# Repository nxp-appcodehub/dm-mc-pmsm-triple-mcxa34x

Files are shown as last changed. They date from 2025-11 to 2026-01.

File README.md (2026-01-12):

# NXP Application Code Hub
[](https://www.nxp.com)

## MCX A34x Triple-Motor and Interleaved PFC Control using an HVP Board

This demo describes the implementation of sensorless triple motor FOC on NXP MCXA346 MCU. Please refer to [AN14805](https://docs.nxp.com/bundle/AN14805/page/topics/introduction.html) for complete instructions on how to use this software. 

#### Boards: X-MCXA346-3MC, dual-motor adapter board
#### Categories: Motor Control
#### Peripherals: PWM, ADC
#### Toolchains: MCUXpresso IDE

## Table of Contents
1. [Software](#step1)
2. [Hardware](#step2)
3. [Setup](#step3)
4. [Results](#step4)
5. [FAQs](#step5) 
6. [Support](#step6)
7. [Release Notes](#step7)

## 1. Software
- Download and install [MCUXpresso IDE V25.06 or later](https://www.nxp.com/design/design-center/software/development-software/mcuxpresso-software-and-tools-/mcuxpresso-integrated-development-environment-ide:MCUXpresso-ID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).
- Download and install the latest version of [FreeMASTER](https://www.nxp.com/design/software/development-software/freemaster-run-time-debugging-tool:FREEMASTER)(3.2.2.2).
- Download the code from Git repository dm-mc-pmsm-triple-mcxa34x.  
- MCUXpresso for Visual Studio Code: This example supports MCUXpresso for Visual Studio Code, for more information about how to use Visual Studio Code please refer [here](https://www.nxp.com/design/training/getting-started-with-mcuxpresso-for-visual-studio-code:TIP-GETTING-STARTED-WITH-MCUXPRESSO-FOR-VS-CODE).

## 2. Hardware
- X-MCXA346-3MC
- 2 pcs [FRDM-MC-LVPMSM](https://www.nxp.com/design/development-boards/freedom-development-boards/mcu-boards/nxp-freedom-development-platform-for-low-voltage-3-phase-pmsm-motor-control:FRDM-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).
- 2 [LINIX 45ZWN24 Motor](https://www.nxp.com/design/development-boards/freedom-development-boards/mcu-boards/low-voltage-3-phase-motor-for-frdm-platform:FRDM-MC-LVMTR).
- 1 pcs dual-motor adapter board
- 1 DL71-PS11M2-1.5K PMSM High-Voltage motor

- Personal Computer
- USB type-C cable and 24V adaptors × 2.

## 3. Setup
### 3.1 Import project
#### 3.1.A Import project from Application Code Hub
1. Open MCUXpresso IDE, in the Quick Start Panel, choose **Import from Application Code Hub** 
2. Found demo you need by searching the name directly or selecting tags you interested in. Open the project, click the **GitHub link** to then **Next**. 
3. Select **main** branch and then click **Next**.
4. Select your local path for the repo in **Destination->Directory:** window. The MCUXpresso IDE will clone the repo to the path that your selected, **Next** after the clone process.
5. Select **Import existing Eclipse projects** in **Wizard for project import** window then **Next**. 
6. Select the project in this repo(only one project in this repo) then **Finish**. 
#### 3.1.B Import project after clone git repo to your local path
1. Clone repo **dm-mc-pmsm-triple-mcxa34x ** from **GitHub**. Open MCUXpresso IDE, in the Quick Start Panel, choose **Import project(s) from file system** .
2. Select your local path of the repo in **Project directory(unpacked)** item then **Next**. If you download a compressed pack from GitHub, Select your local path of the package in **Project archive(zip)** item.
3. Select the project in this repo(show in **Projects:** window, only one project in this repo), then **Finish**. . The project will be pasted to your IDE workspace if you click **Copy projects into workspace** in **Options** item, the change you made will be saved in the copy in workspace.
#### 3.1.2 Then you will see the project in **Project Explorer** window.
### 3.2 Compiler the project

This project contains 3 configurations, **Debug**, **Release** and **Debug_SRAMX**. **Release** configuration has a standalone link script to allocate frequently called code in SRAMX to improve performance. **Right click** the project name in **Project Explorer** window, and select **Properties** to open properties window. Open **Manage Configurations**, select configuration you want to use then **Set Active**.  
 
Use build botton in toolbar to compiler the project.  

### 3.3 Hardware setup
#### 3.3.1 Connect the motor and power shield board.
 Connect the 3-phase wire of the **first motor** to the **J7** connector on the **first FRDM-MC-LVPMSM** according to phase sequence (**White** wide--phase**A**; **Bule** wide--phase**B**; **Green** wide--phase**C**). Repeat the same steps for the **second motor** and **second FRDM-MC-LVPMSM**.

#### 3.3.2 Combine the motor kit with adaptor board.
Connect the **first FRDM-MC-LVPMSM** board to the **J1_M1~J4_M1** arduino connector of the **NXP Dual Motor Adaptor Board**. And connect the **second FRDM-MC-LVPMSM** board to the **J1_M2~J4_M2** arduino connector of the adaptor board. The **X-MCXA346-3MC** daughter board **J9 and J8** is connected to the **2 IDC-20Pin socket** on the adaptor board. The GERBER file and schematic of the adaptor are in path **dm-mc-pmsm-triple-mcxa34x/schematic_pcb**.

#### 3.3.3 Rework
Rework HVP board resistor **R128** to **680Ω**

#### 3.3.4 Connect daughter board and High-Voltage motor to HVP
Connect X-MCXA346-3MC daughter board to HVP board PCI socket, connect High-Voltage motor to HVP J13.

#### 3.3.5 Download and Power up
Power 2 FRDM-MC-LVPMSM boards with two 24V adaptor.  
Use a USB cable to connect to the X-MCXA346-3MC board via **J2** Download the code using debug button in tool bar after compiler. Select **CMSIS-DAP** in **Debug As** according firmware in your on-board debugger. Then unplug the USB cable and power up the HVP board with AC 220V power line.

### 3.4 Run the demo
Connect HVP board with PC through USB plugged on  **J4** on **HVP** to control the **Motor M1~M3** to run or stop, use FreeMASTER project **"pmsm_float.pmpx"** in the package path **"dm-mc-pmsm-triple-mcxa34x\motor_control\freemaster"** to control the motor, change rotor speed and obverse the speed or other value. 
## 4. Results

Memory Usage:
|Debug Configuration|Flash Usage|SRAM usage|SRAMX usage|
|:----:|:----:|:----:|:----:|
|All code in Flash|65.9 KB|30.3 KB|0 KB|
|Partial code in SRAM/SRAMX |66.3 KB |35.2 KB | 4.4 KB |

CPU loading:
|Debug Configuration|Flash Usage|SRAM usage|SRAMX usage|
|:----:|:----:|:----:|:----:|
|All code in Flash|65.38 %|2.98 %|68.36 %|
|Partial code in SRAM/SRAMX |30.09 %|1.14 %|31.23 %|

## 5. Support

#### Project Metadata

<!----- Boards ----->

<!----- Categories ----->


<!----- Peripherals ----->



<!----- Toolchains ----->


Questions regarding the content/correctness of this example can be entered as Issues within this GitHub repository.

>**Warning**: For more general technical questions regarding NXP Microcontrollers and the difference in expected functionality, enter your questions on the [NXP Community Forum](https://community.nxp.com/)






## 7. Release Notes
| Version | Description / Update | Date |
|:---:|---|---:|
| 1.0 | Initial release on Application Code Hub | November 11<sup>th</sup> 2025 |

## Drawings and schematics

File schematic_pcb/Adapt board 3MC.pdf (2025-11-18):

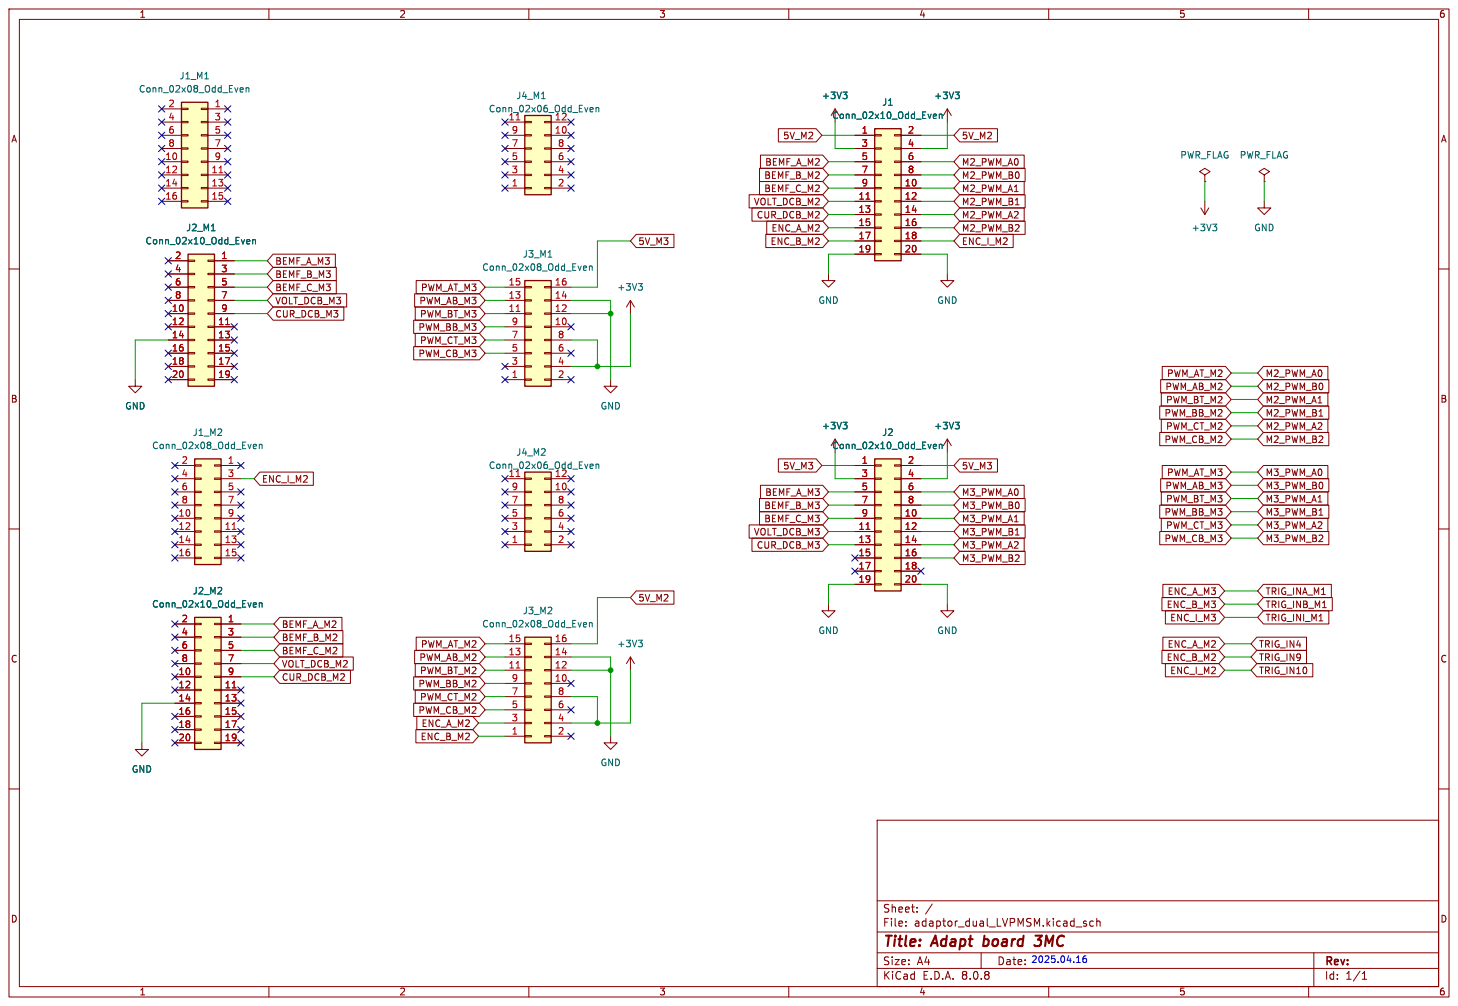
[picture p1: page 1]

Id: 1/1 Title: Adapt board 3MC

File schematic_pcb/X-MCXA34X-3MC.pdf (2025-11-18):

Initial release | Jonson Chen

# Revisions

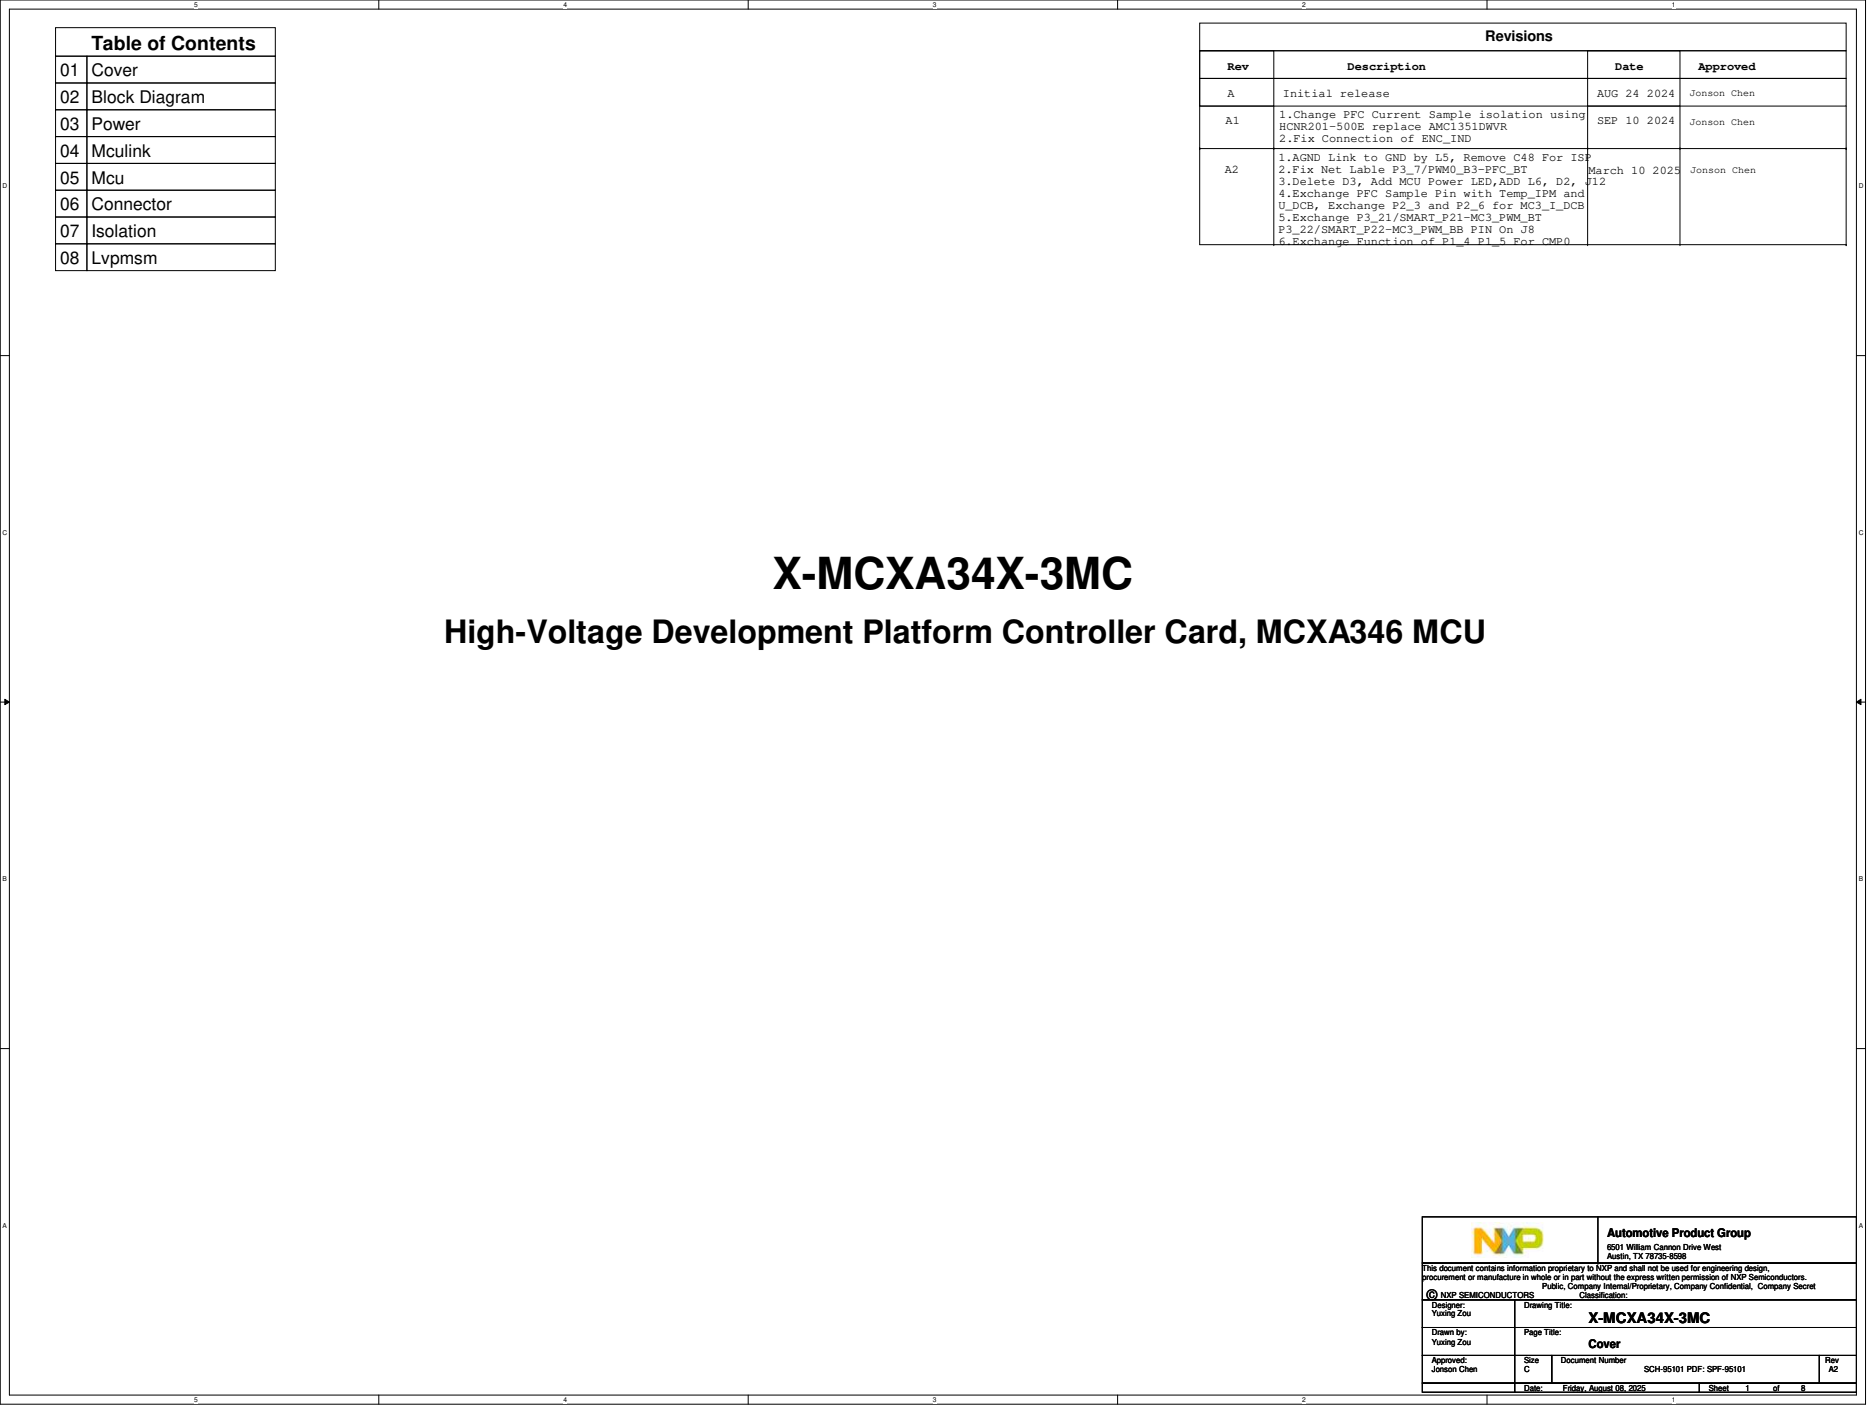
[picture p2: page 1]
Description; Rev; Date; Approved; AUG 24 2024; X-MCXA34X-3MC; 1.Change PFC Current Sample isolation using HCNR201-500E replace AMC1351DWVR; SEP 10 2024; Jonson Chen; 3.Delete D3, Add MCU Power LED,ADD L6, D2,; March 10 2025; Table of Contents; 01 Cover; 02 Block Diagram; 03 Power; 04 Mculink; 05 Mcu; 06 Connector; 07 Isolation; 08 Lvpmsm; Drawing Title:; Size; Document Number; Date:; Sheet; Page Title:; Drawn by:; Approved:; © NXP SEMICONDUCTORS; Classification:; SCH-95101 PDF: SPF-95101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

2.Fix Connection of ENC_IND
1.AGND Link to GND by L5, Remove C48 For ISP
2.Fix Net Lable P3_7/PWM0_B3-PFC_BT
4.Exchange PFC Sample Pin with Temp_IPM and
U_DCB, Exchange P2_3 and P2_6 for MC3_I_DCB
5.Exchange P3_21/SMART_P21-MC3_PWM_BT
P3_22/SMART_P22-MC3_PWM_BB PIN On J8
6.Exchange Function of P1_4 P1_5 For CMP0

High-Voltage Development Platform Controller Card, MCXA346 MCU

Automotive Product Group

6501 William Cannon Drive West
Austin, TX 78735-8598

This document contains information proprietary to NXP and shall not be used for engineering design,
procurement or manufacture in whole or in part without the express written permission of NXP Semiconductors.
Designer:
Yuxing Zou

Public, Company Internal/Proprietary, Company Confidential, Company Secret

# MCXA34X-3MC

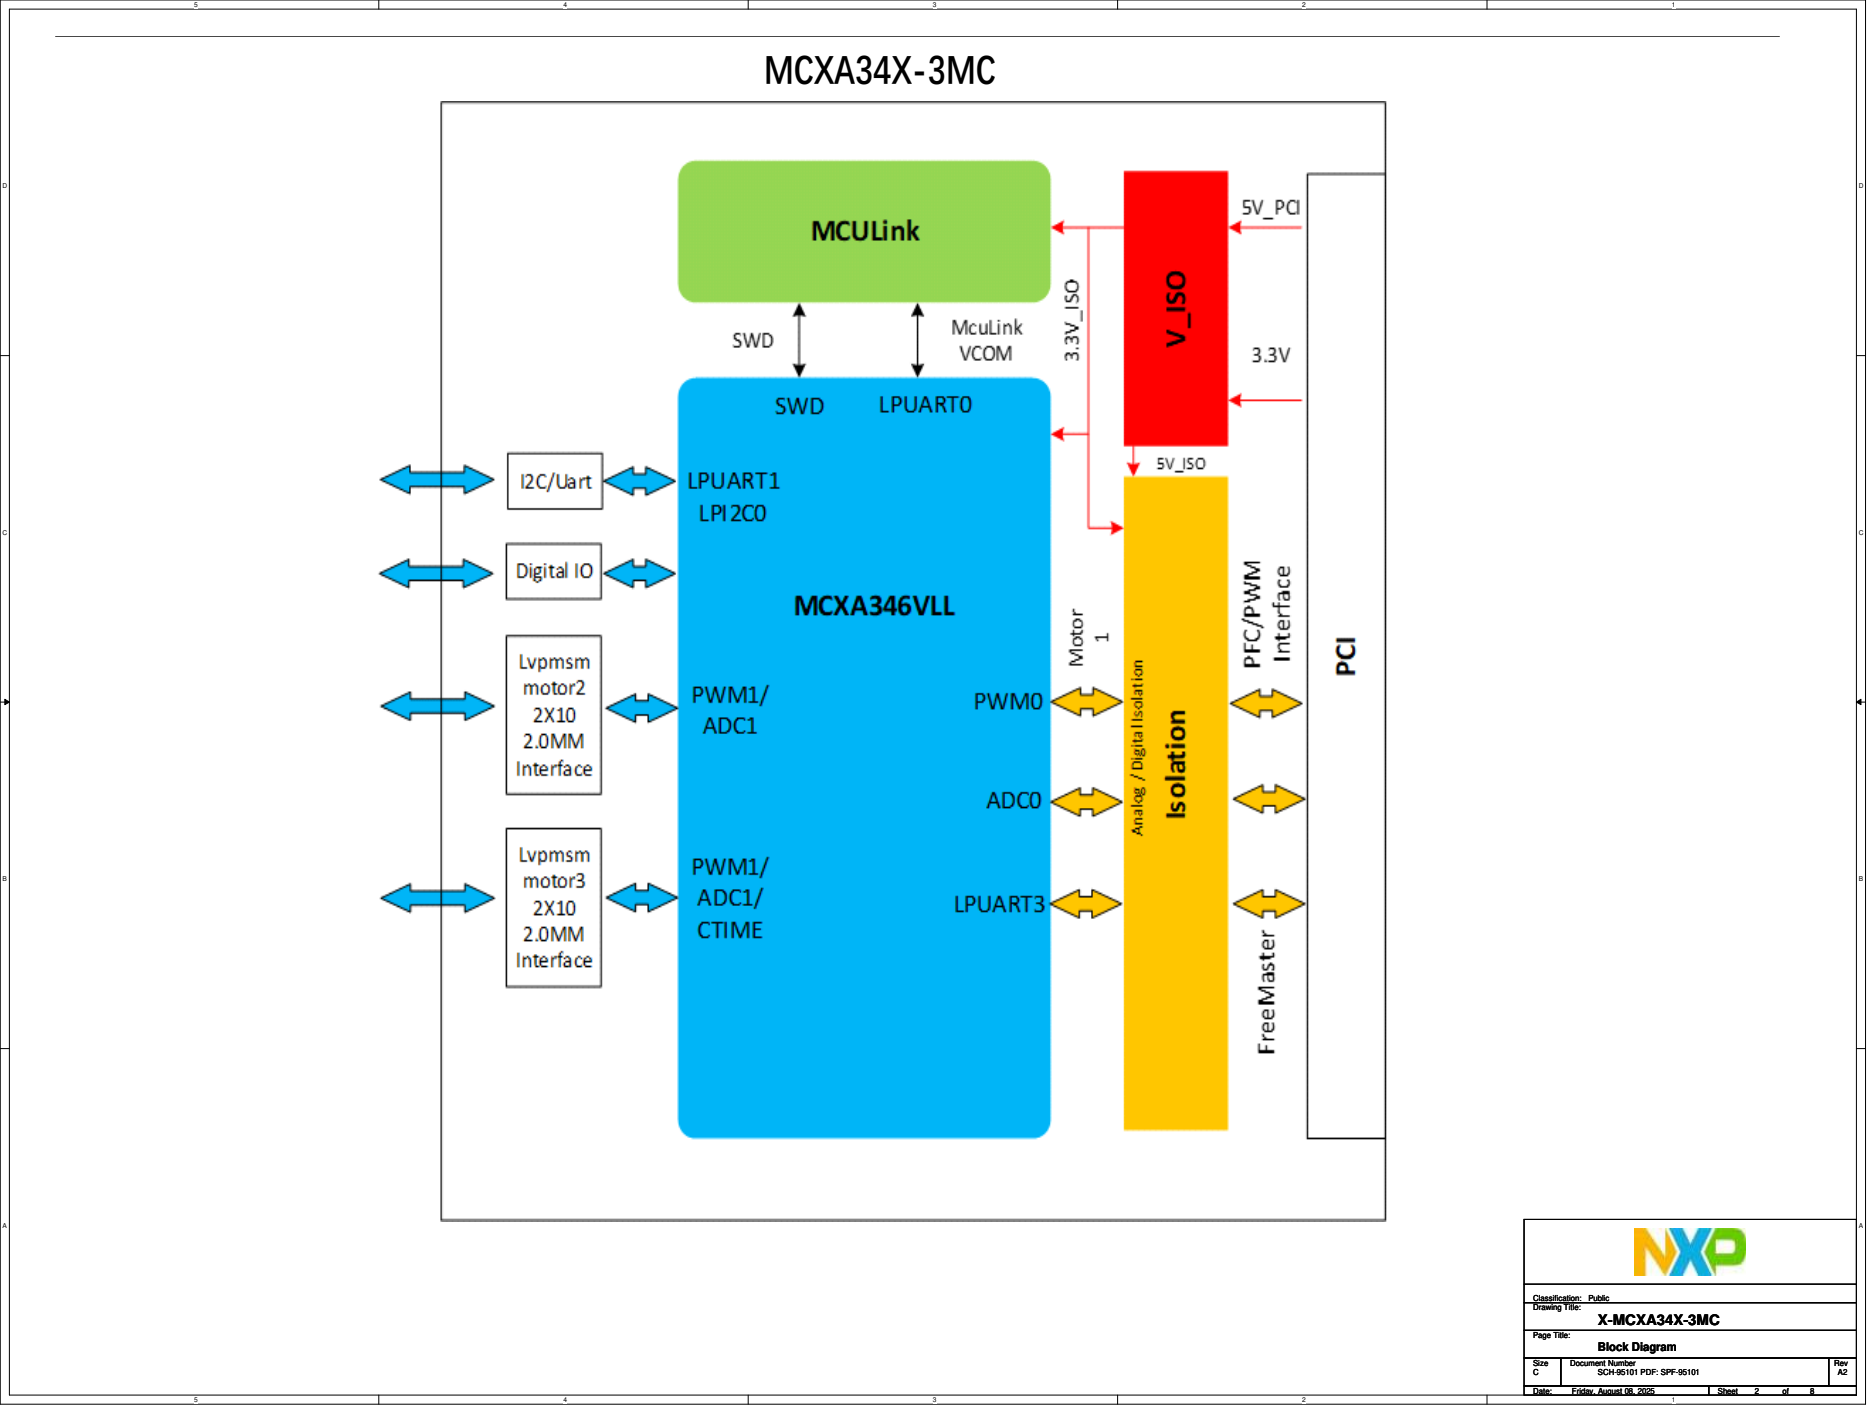
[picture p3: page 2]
Classification:; Block Diagram; Public

SCH-95101 PDF: SPF-95101

# Galvanic isolated part. Isolation = 8mm Creepage and clearence (5kV)

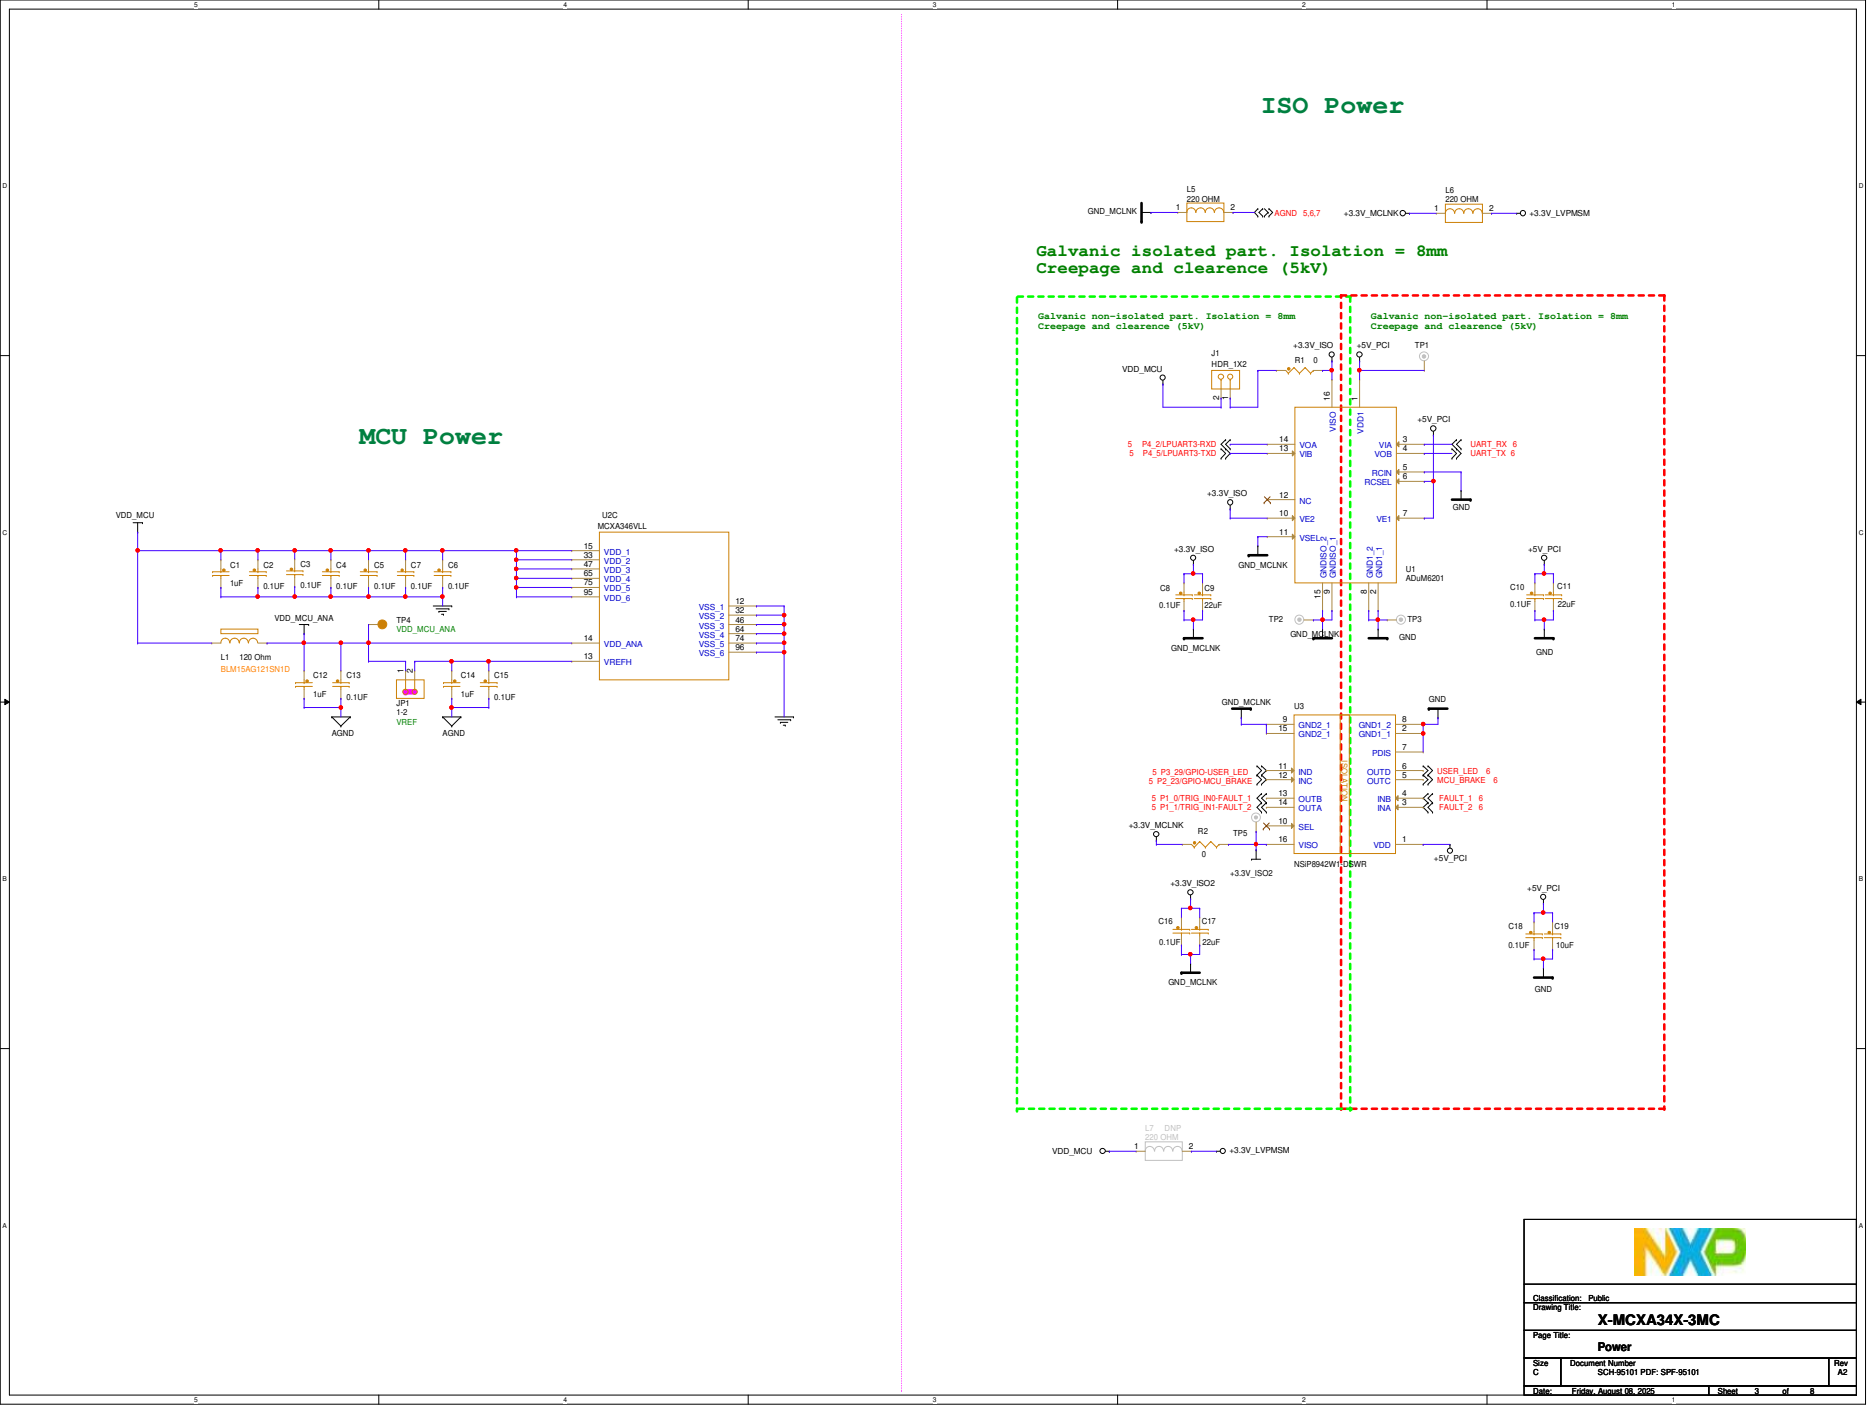
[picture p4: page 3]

Galvanic non-isolated part. Isolation = 8mm
Creepage and clearence (5kV)

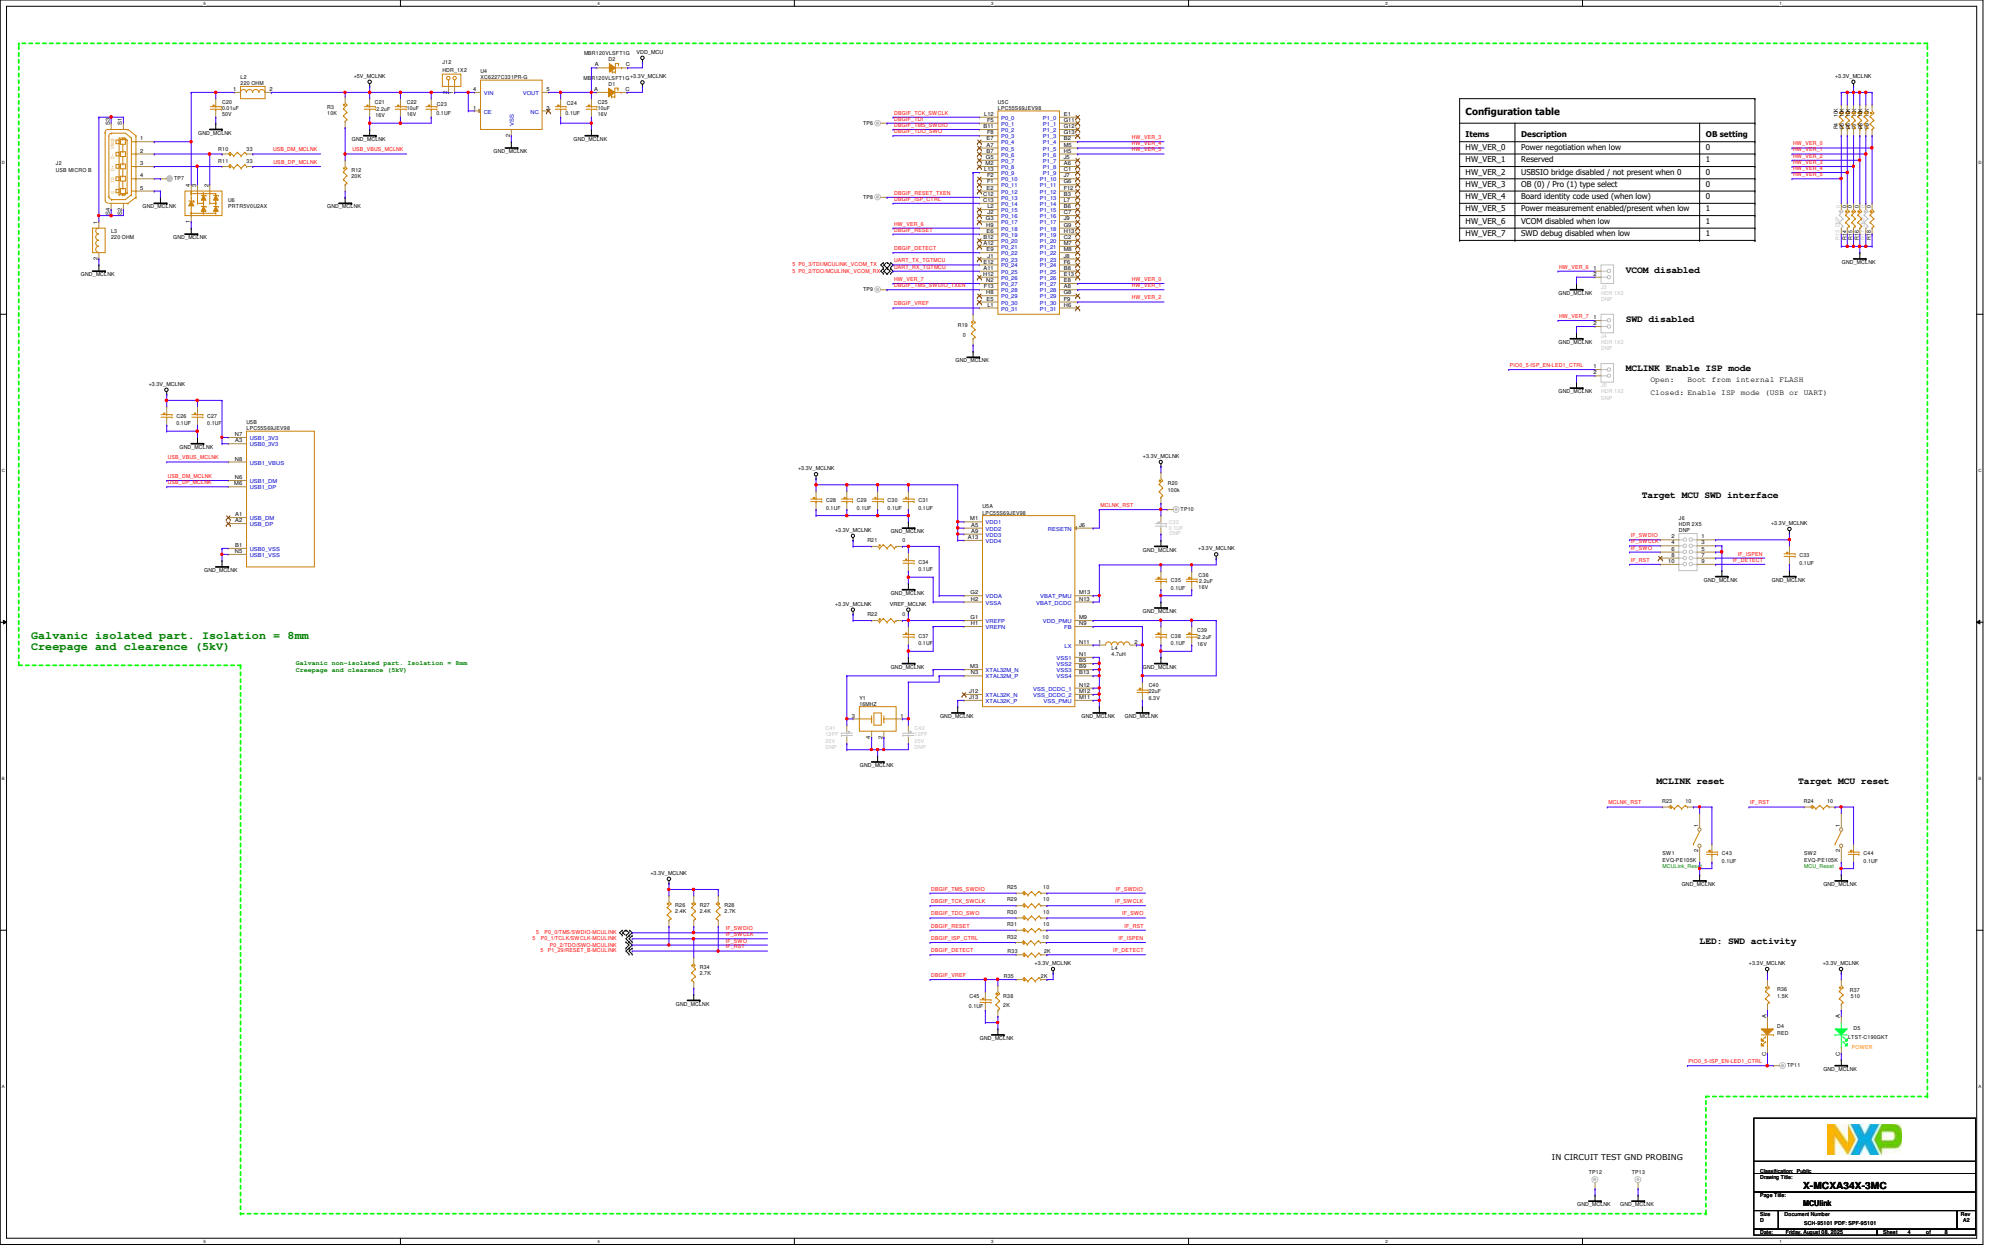
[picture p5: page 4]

VBUSD-D+IDG USB MICRO B J2 1234

HW_VER_0 | Power negotiation when low | 0
HW_VER_1 | Reserved | 1
HW_VER_2 | USBSIO bridge disabled / not present when 0 | 0
HW_VER_3 | OB (0) / Pro (1) type select | 0
HW_VER_4 | Board identity code used (when low) | 0
HW_VER_5 | Power measurement enabled/present when low | 1
HW_VER_6 | VCOM disabled when low | 1

HW_VER_7 | SWD debug disabled when low | 1

MCLINK Enable ISP mode

Boot from internal FLASH
Enable ISP mode (USB or UART)

Target MCU SWD interface

Galvanic isolated part. Isolation = 8mm
Creepage and clearence (5kV)

Galvanic non-isolated part. Isolation = 8mm

IN CIRCUIT TEST GND PROBING

# MCU CLOCK

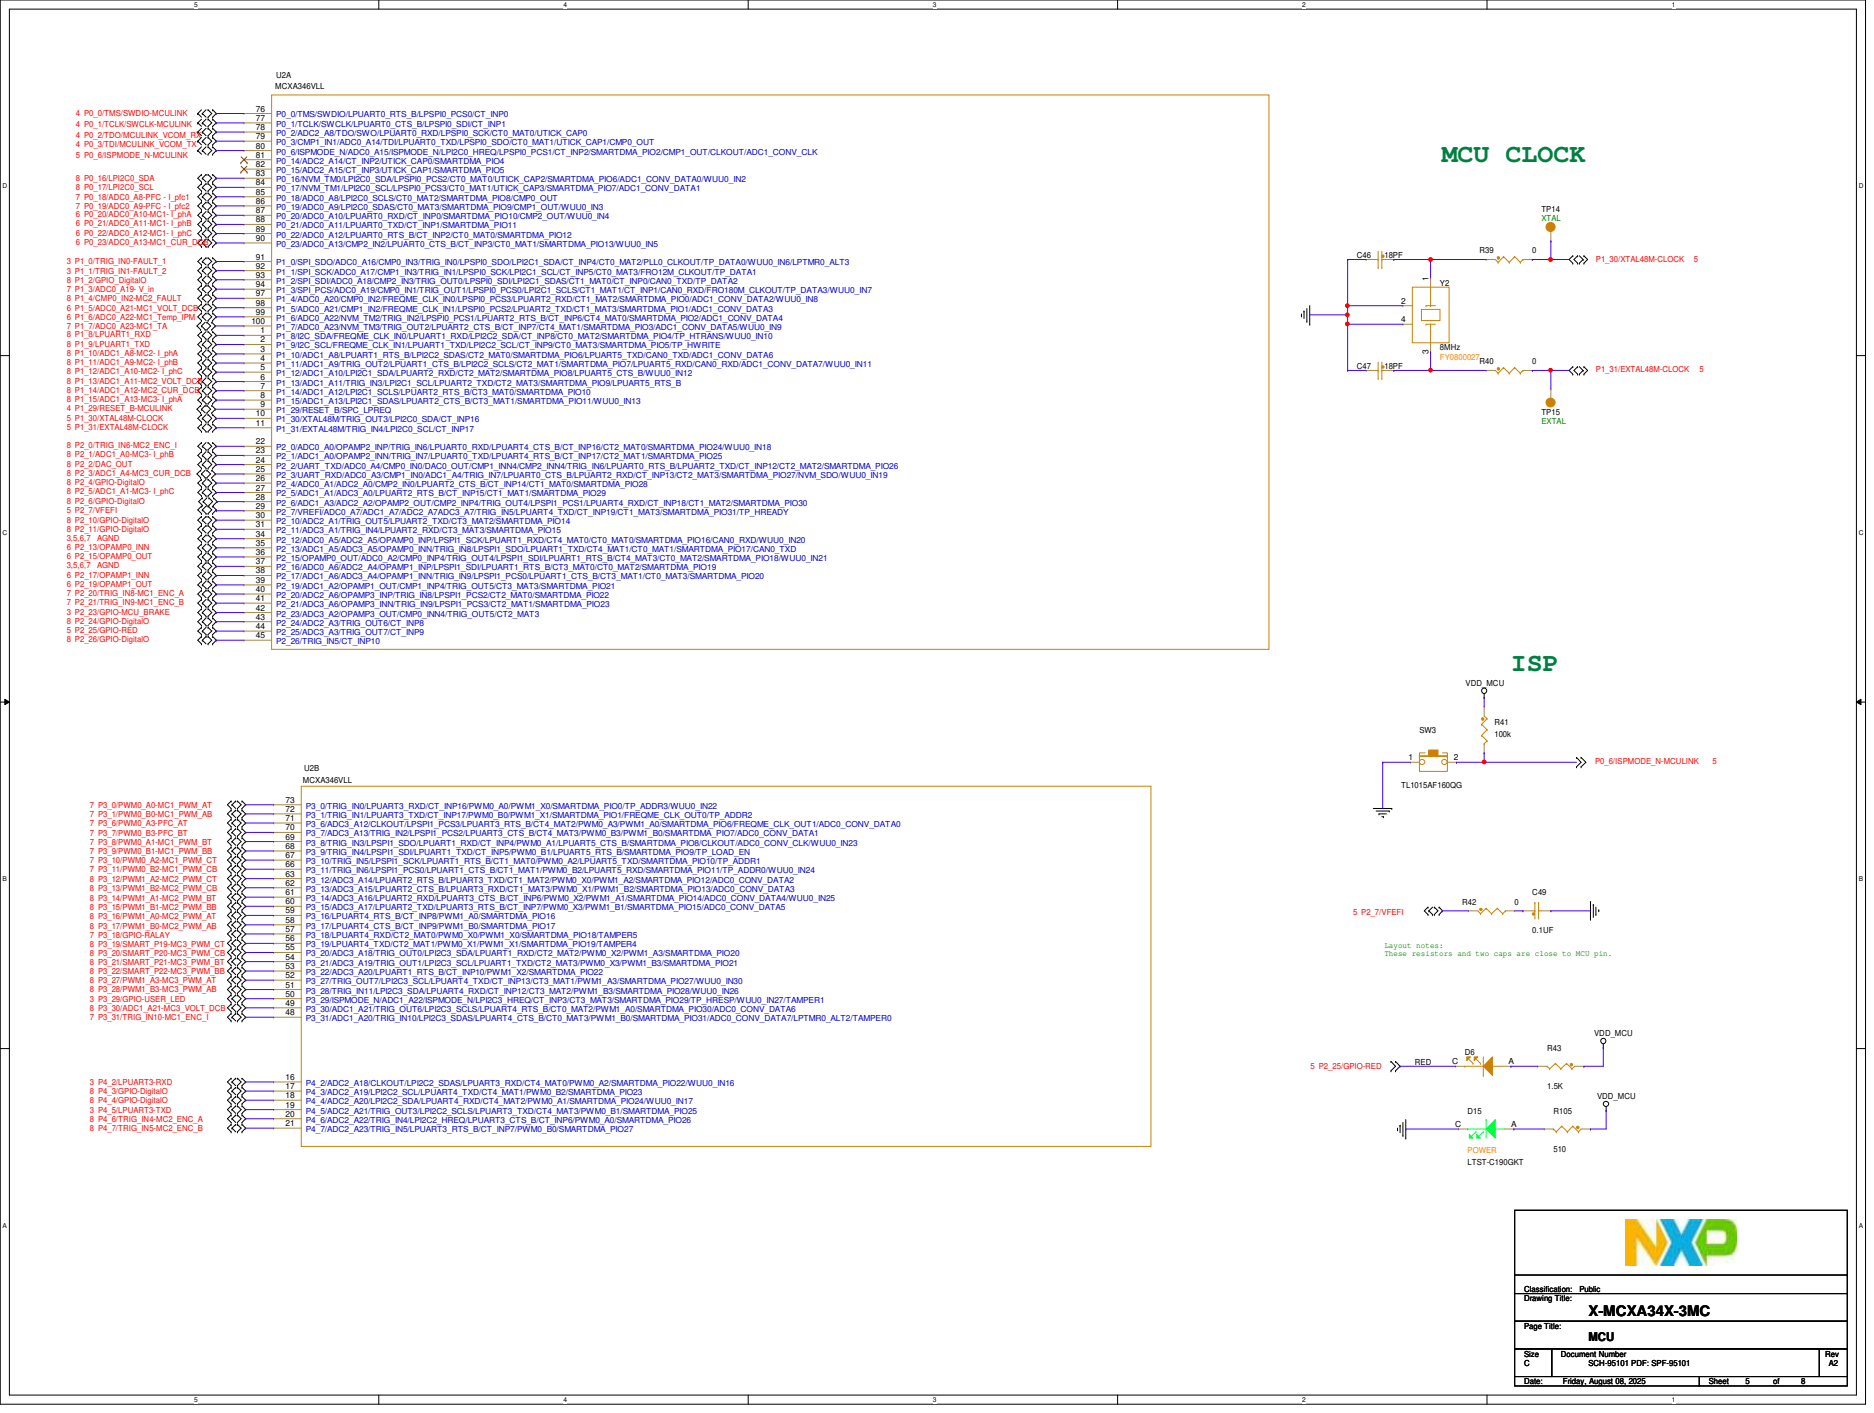
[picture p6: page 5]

Layout notes:
These resistors and two caps are close to MCU pin.

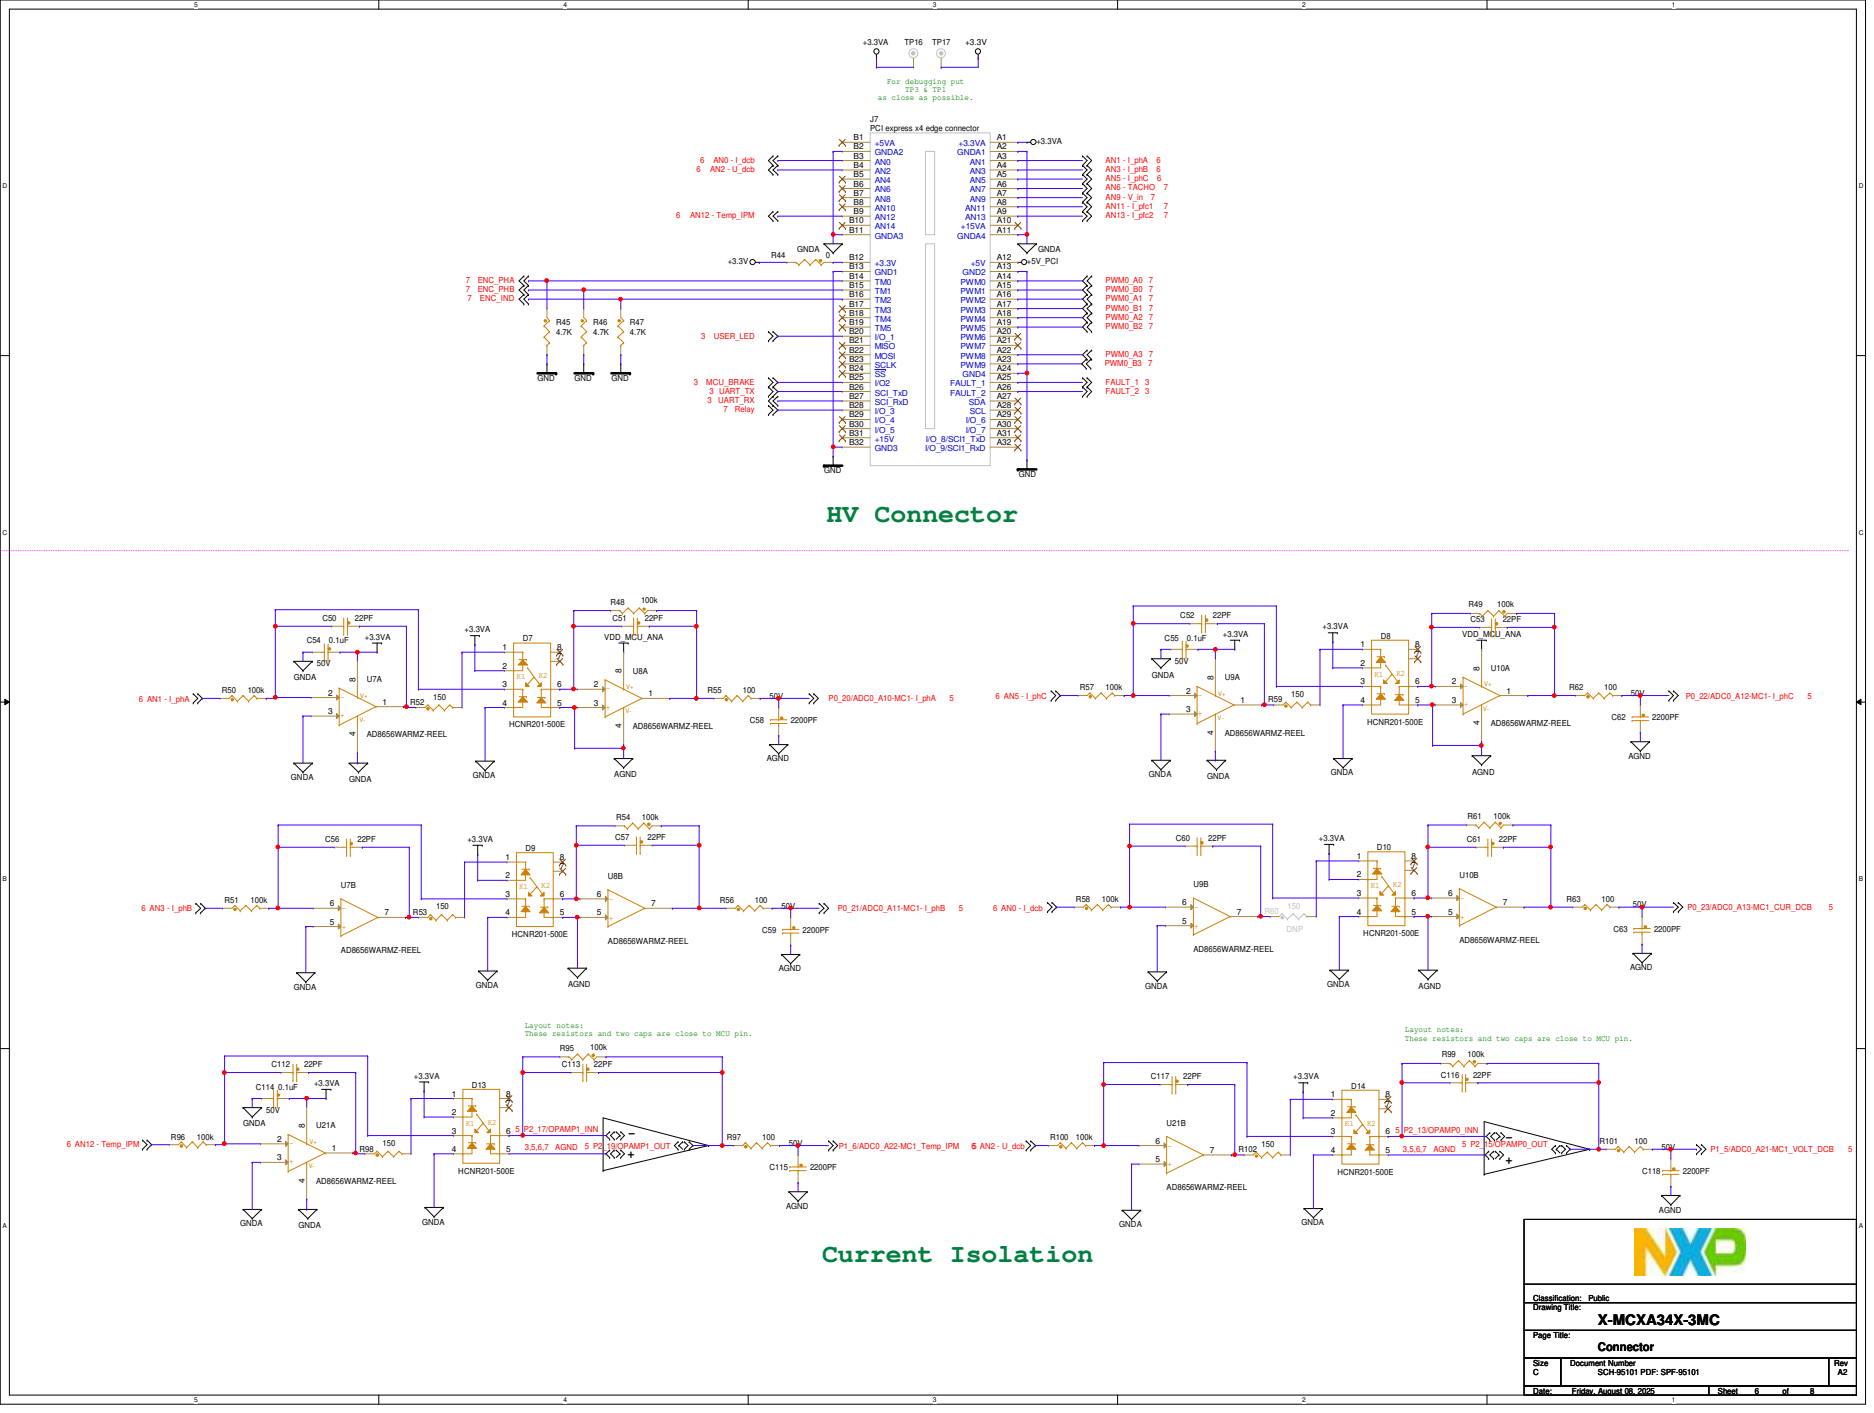
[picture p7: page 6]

as close as possible.

Layout notes:
These resistors and two caps are close to MCU pin.

DIGITAL ISOLATION | ANALOG ISOLATION

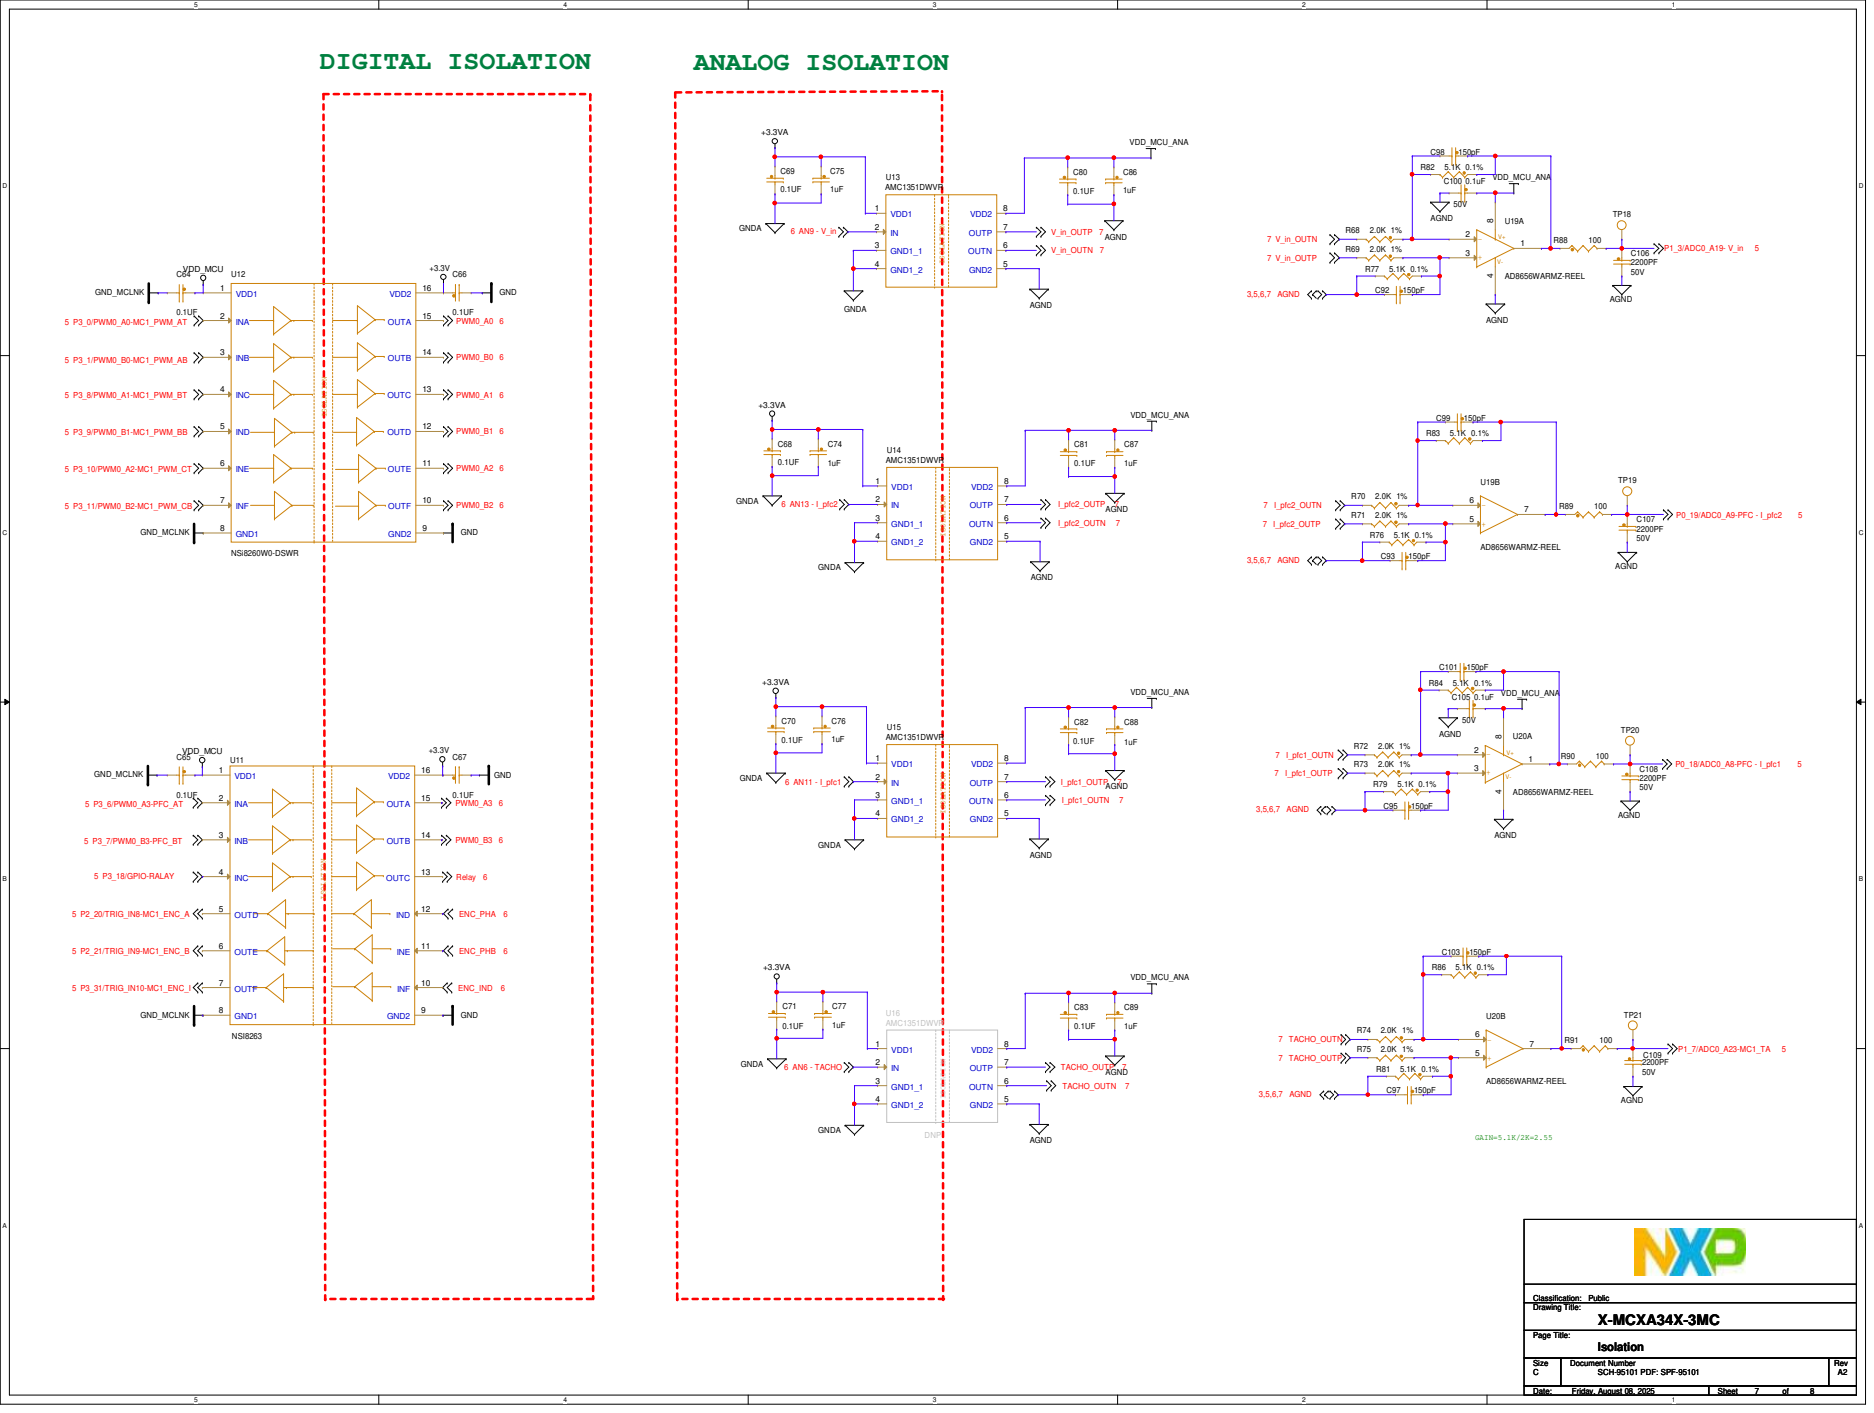
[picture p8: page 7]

# LV Motor Interface

+3.3V_LVPMSM | +3.3V_LVPMSM

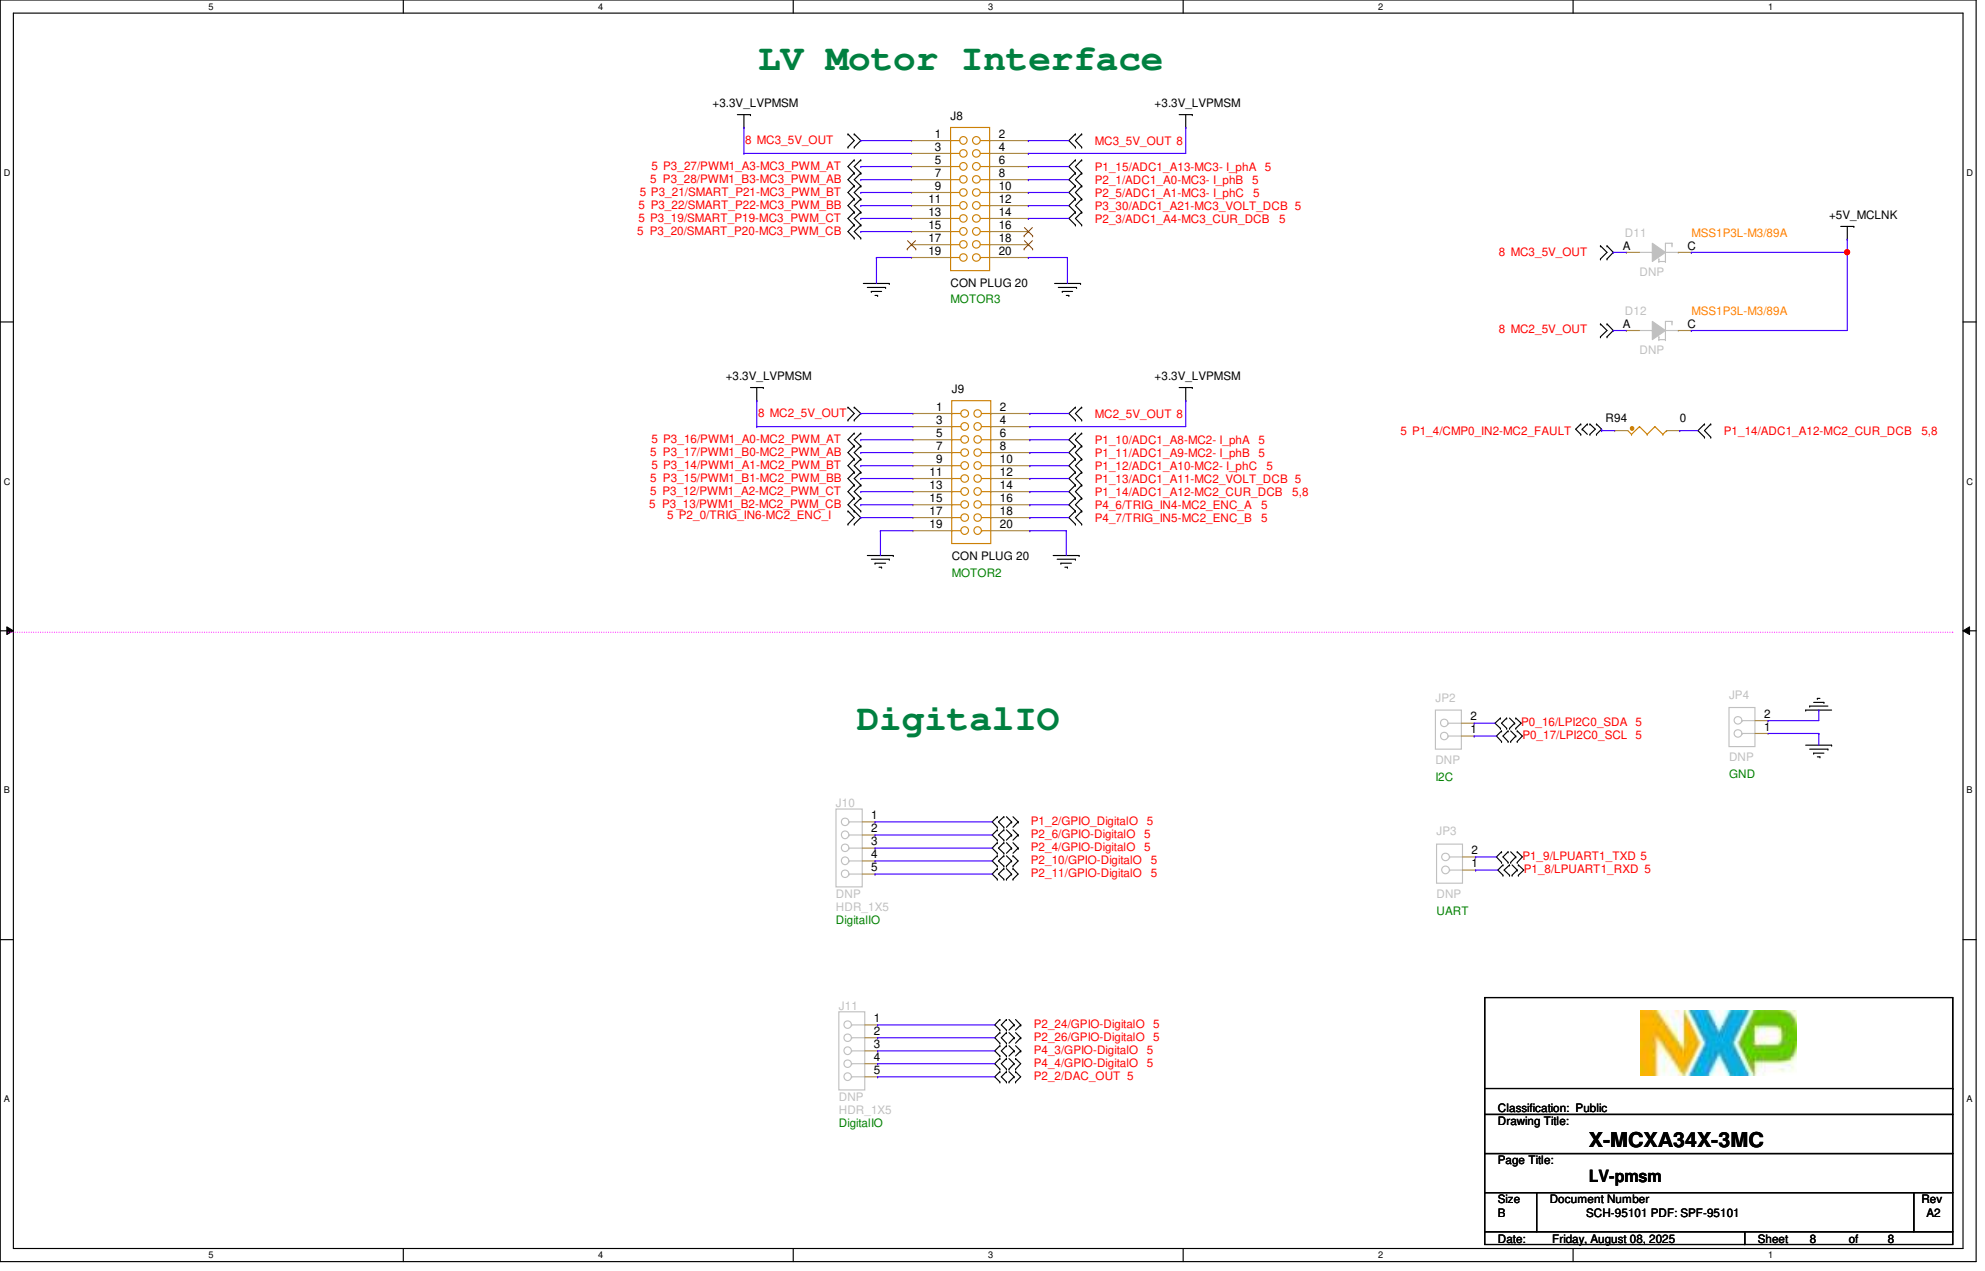
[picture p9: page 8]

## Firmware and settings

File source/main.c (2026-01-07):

/*
 * Copyright 2019 NXP
 * All rights reserved.
 *
 * SPDX-License-Identifier: BSD-3-Clause
 */

#include "board.h"
#include "hardware_init.h"
#include "mc_periph_init.h"
#include "freemaster.h"
#include "freemaster_serial_lpuart.h"
#include "m1_sm_snsless.h"
#include "m2_sm_snsless.h"
#include "m3_sm_snsless.h"
#include "PFC_statemachine.h"
#include "fsl_lpuart.h"
#include "fsl_debug_console.h"
#include "fsl_lptmr.h"
#include "fsl_smartdma.h"
#include "fsl_smartdma_mcxa.h"
/*******************************************************************************
 * Definitions
 ******************************************************************************/
/* Version info */
#define MCRSP_VER "2.0.0" /* motor control package version */

/* Example's feature set in form of bits inside ui16featureSet.
   This feature set is expected to be growing over time.
   ... | FEATURE_S_RAMP | FEATURE_FIELD_WEAKENING | FEATURE_ENC
*/
#define FEATURE_ENC (1)               /* Encoder feature flag */
#define FEATURE_FIELD_WEAKENING (0)   /* Field weakening feature flag */
#define FEATURE_S_RAMP (0)            /* S-ramp feature flag */

#define FEATURE_SET (FEATURE_ENC << (0) | \
                     FEATURE_FIELD_WEAKENING << (1) | \
                     FEATURE_S_RAMP << (2))

/* CPU load measurement SysTick START / STOP macros */
#define SYSTICK_START_COUNT() (SysTick->VAL = SysTick->LOAD)
#define SYSTICK_STOP_COUNT(par1)   \
    uint32_t val  = SysTick->VAL;  \
    uint32_t load = SysTick->LOAD; \
    par1          = load - val

/* CPU load measurement using Systick */
uint32_t g_ui32NumberOfCycles    = 0U;
uint32_t g_ui32MaxNumberOfCycles = 0U;

/*******************************************************************************
 * Prototypes
 ******************************************************************************/
static void BOARD_InitSysTick(void);
void SmartDMA_pwm_fault_callback(void *param);
/*******************************************************************************
 * Variables
 ******************************************************************************/
/* Structure used in FM to get required ID's */
app_ver_t g_sAppIdFM = {
    "MCXA346", /* board id */
    "X-MCXA346-3MC", /* example id */
    MCRSP_VER,      /* sw version */
    FEATURE_SET,    /* example's feature-set */
};

uint32_t        M1_isr_cnt=0;
uint32_t        M2_isr_cnt=0;
uint32_t        M3_isr_cnt=0;
uint32_t        PFC_isr_cnt=0;
uint32_t        Slow_isr_cnt=0;
/*******************************************************************************
 * Variables
 ******************************************************************************/
/* Whether the SW button is pressed */
volatile bool g_ButtonPress = false;
smartdma_pwm_fault_param_t smartdmaParam;                  /*!< SMARTDMA function parameters. */
volatile uint8_t g_samrtdma_stack[32];
volatile uint32_t g_pwm_gpio_register[8] = {
		0x400BF000 + 0x80 + 25*4,/*PWM_AT, P3_27,Pin Control Register*/
		0x400BF000 + 0x80 + 26*4,/*PWM_AB, P3_28,Pin Control Register*/
		0x400BF000 + 0x80 + 21*4,/*PWM_BT, P3_21,Pin Control Register*/
		0x400BF000 + 0x80 + 22*4,/*PWM_BB, P3_22,Pin Control Register*/
		0x400BF000 + 0x80 + 19*4,/*PWM_CT, P3_19,Pin Control Register*/
		0x400BF000 + 0x80 + 20*4,/*PWM_CB, P3_20,Pin Control Register*/
};
/*******************************************************************************
 * Code
 ******************************************************************************/
/*!
 * @brief Main function
 */
void main(void)
{
    /*Accessing ID structure to prevent optimization*/
    g_sAppIdFM.ui16FeatureSet = FEATURE_SET;
    
    SYSCON->NVM_CTRL &= ~SYSCON_NVM_CTRL_DIS_MBECC_ERR_DATA_MASK;
    SYSCON->LPCAC_CTRL |= SYSCON_LPCAC_CTRL_LPCAC_MEM_REQ_MASK;
    SYSCON->LPCAC_CTRL &= ~SYSCON_LPCAC_CTRL_DIS_LPCAC_MASK;
    
    uint32_t ui32PrimaskReg;

    /* Disable all interrupts before peripherals are initialized */
    ui32PrimaskReg = DisableGlobalIRQ();
    
    /* Board pin init */
    BOARD_InitHardware();
         
    SMARTDMA_InitWithoutFirmware();
    SMARTDMA_InstallFirmware(SMARTDMA_PWM_FAULT_MEM_ADDR,s_smartdmaPWMFaultFirmware,
    SMARTDMA_PWM_FAULT_FIRMWARE_SIZE);
    NVIC_EnableIRQ(SMARTDMA_IRQn);
    NVIC_SetPriority(SMARTDMA_IRQn, 3);
    SMARTDMA_InstallCallback(SmartDMA_pwm_fault_callback, NULL);
    smartdmaParam.smartdma_stack 	 = (uint32_t*)g_samrtdma_stack;
    smartdmaParam.p_gpio_reg  		 = (uint32_t*)g_pwm_gpio_register;
    SMARTDMA_Boot(kSMARTDMA_pwm_fault, &smartdmaParam, 0x2);    
    /* Initialize peripheral motor control and PFC driver */
    MCDRV_Init();
    BOARD_InitDebugConsole();
    
    /* FreeMASTER driver initialization */
    FMSTR_Init();
    FMSTR_Recorder_Create();
    
    /* SysTick initialization for CPU load measurement */
    BOARD_InitSysTick();
    
    //PWM counter must run just before IRQ enable
    FLEXPWM0->MCTRL = (FLEXPWM0->MCTRL & ~PWM_MCTRL_RUN_MASK) | PWM_MCTRL_RUN(0xF);
    FLEXPWM1->MCTRL = (FLEXPWM1->MCTRL & ~PWM_MCTRL_RUN_MASK) | PWM_MCTRL_RUN(0xF);
    
    /* Enable interrupts */
    EnableGlobalIRQ(ui32PrimaskReg);

    while (1)
    {
      /* FreeMASTER Polling function */
      FMSTR_Poll();
    }
}

//ADC0 interrupt for compressor sample, priority 4
void ADC0_IRQHandler(void)
{
    /* Clear the TCOMP INT flag */
    ADC0->STAT |= (uint32_t)(1U << 9);
    
    /* Transfer the UDCB voltage for Compressor control */
    g_sM1Drive.sFocPMSM.fltUDcBusFilt = gsPFC_Drive.sUCtrl.fltUDcBusFilt;

    /* StateMachine call */
    SM_StateMachineFast(&g_sM1Ctrl);

    /* Call FreeMASTER recorder */
    FMSTR_Recorder(0);
    __DSB();
    __ISB();
}

int16_t pwm0_counter;
void ADC1_IRQHandler(void)
{
    /* Clear the TCOMP INT flag */
    ADC1->STAT |= (uint32_t)(1U << 9);
    

    pwm0_counter = FLEXPWM0->SM[0].CNT;
    
    if(pwm0_counter<0)
    {
    	M2_isr_cnt++;

    	/* StateMachine call */
    	SM_StateMachineFast(&g_sM2Ctrl);
      
    }
    else
    {
      M3_isr_cnt++;

      /* StateMachine call */
      SM_StateMachineFast(&g_sM3Ctrl);

    }

    __DSB();
    __ISB();
    
}

int cntt=0;
void LPTMR0_IRQHandler(void)
{
	static int isr_cnt = 0;

	if(++isr_cnt==1000)
	{
		isr_cnt = 0;
		GPIO_PortToggle(GPIO2, 1<<25);
	}
  /* Clear the match interrupt flag. */
    LPTMR_ClearStatusFlags(LPTMR0, kLPTMR_TimerCompareFlag);

    if(4 == cntt++)
    {
      /* M1 Slow StateMachine call */
      SM_StateMachineSlow(&g_sM1Ctrl);
    
      /* M2 Slow StateMachine call */
      SM_StateMachineSlow(&g_sM2Ctrl);
      
      /* M3 Slow StateMachine call */
      SM_StateMachineSlow(&g_sM3Ctrl);

      cntt=0;      
    }
    
#if 1
    gsPFC_Drive.sUCtrl.fltUDcBus = gsPFC_Drive.sUInPeakDetection.fltUdcb;
    gsPFC_Drive.sUCtrl.fltUDcBusFilt = GDFLIB_FilterIIR1_FLT(gsPFC_Drive.sUCtrl.fltUDcBus, &gsPFC_Drive.sUCtrl.sUDcBusFilter);

    PFC_UInPeak_detect(&gsPFC_Drive);

    //PFC control
    SM_StateMachineSlow(&gsPFC_Ctrl);
    
#endif

    __DSB();
    __ISB();
}

void CTIMER4_IRQHandler(void)
{
    /* Clear the match interrupt flag. */
    CTIMER4->IR |= CTIMER_IR_MR2INT(1U);
   
    CTIMER4->TCR = CTIMER_TCR_CRST_MASK;
    CTIMER4->TCR = 0;
    CTIMER4->TCR = CTIMER_TCR_ATCEN_MASK;
    
    PFC_isr_cnt++;
    
    //GPIO4->PSOR |= 1<<4;
    
    PFC_MCDRV_ADC_GET(&g_sPFCAdcSensor);
      
    gsPFC_Drive.sICtrlPh1.fltIFdbck = 
      MLIB_ConvSc_FLTsf(MLIB_Sub_F16(gsPFC_Drive.sUInPeakDetection.f16Imos2, gsPFC_Drive.sUInPeakDetection.f16Offset2), g_fltPFCCurrentScale);
   
    gsPFC_Drive.sICtrlPh2.fltIFdbck = 
      MLIB_ConvSc_FLTsf(MLIB_Sub_F16(gsPFC_Drive.sUInPeakDetection.f16Imos1, gsPFC_Drive.sUInPeakDetection.f16Offset2), g_fltPFCCurrentScale);
    
    
    if(gsPFC_Drive.sICtrlPh1.fltIFdbck<0) gsPFC_Drive.sICtrlPh1.fltIFdbck=0;
    if(gsPFC_Drive.sICtrlPh2.fltIFdbck<0) gsPFC_Drive.sICtrlPh2.fltIFdbck=0;
    
    gsPFC_Drive.sUInPeakDetection.fltUInFiltRaw = GDFLIB_FilterIIR1_FLT(gsPFC_Drive.sUInPeakDetection.fltUIn, &gsPFC_Drive.sUInPeakDetection.sFilter);
    gsPFC_Drive.sUInPeakDetection.fltUInFilt = MLIB_Abs_FLT(gsPFC_Drive.sUInPeakDetection.fltUInFiltRaw);
    
    #if PLL
    PFC_Phase_detect(&gsPFC_Drive);
    #endif
      
    SM_StateMachineFast(&gsPFC_Ctrl);
    
    __DSB();
    __ISB();
}

static void BOARD_InitSysTick(void)
{
    /* Initialize SysTick core timer to run free */
    /* Set period to maximum value 2^24*/
    SysTick->LOAD = 0xFFFFFF;

    /*Clock source - System Clock*/
    SysTick->CTRL |= SysTick_CTRL_CLKSOURCE_Msk;

    /*Start Sys Timer*/
    SysTick->CTRL |= SysTick_CTRL_ENABLE_Msk;
}

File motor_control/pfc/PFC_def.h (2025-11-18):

/*
 * Copyright (c) 2013 - 2015, Freescale Semiconductor, Inc.
 * Copyright 2016-2021 NXP
 * All rights reserved.
 *
 * SPDX-License-Identifier: BSD-3-Clause
 */


#ifndef PFC_DEF_H_
#define PFC_DEF_H_

/******************************************************************************
* Includes
******************************************************************************/
#include "PFC_structure.h"

/******************************************************************************
* Constants
******************************************************************************/

/******************************************************************************
* Macros 
******************************************************************************/
#define PLL                                 1
#define NANO_EDGE_EN                        1
#define BURST_MODE_EN                       1

/*************************************** AC input voltage filter ************************************************/
/* input voltage filter, Fs = 32k, Fc = 2kHz */
#define PFC_U_IN_IIR_B0                     (0.16)
#define PFC_U_IN_IIR_B1                     (0.16)
#define PFC_U_IN_IIR_A1                     (0.68)

/*************************************** AC input voltage peak detection ************************************************/
#define PEAK_DET_INPUT_VOLTAGE_RISE_NUM               8       /* During input voltage peak detection, voltage is considered to be rising when it's been detected rising at least
                                                                 this value of times */
#define PEAK_DET_INPUT_VOLTAGE_FALL_NUM               8       /* During input voltage peak detection, voltage is considered to be falling when it's been detected falling at least
                                                                 this value of times */
#define PEAK_DET_INPUT_VOLTAGE_PEAK_NUM				  8       /* PFC starts to work at least this number of peaks have been detected */

/*************************************** AC input voltage phase detection ************************************************/
#define PHASE_DET_INPUT_VOLTAGE_PERIOD_FILTER_N       2       /* Input AC voltage period MA filter number, which represents 2^number averaging points */
#define PHASE_DET_INPUT_VOLTAGE_PERIOD_FILTER_POINTS  4       /* Input AC voltage period MA filter points = 2^PHASE_DET_INPUT_VOLTAGE_PERIOD_FILTER_N */
#define PHASE_DET_INPUT_VOLTAGE_FALL_CNT_THRSD        3       /* When input AC voltage is falling and the voltage is below threshold, a counter increases in every fast loop. 
                                                               The falling edge input voltage threshold is considered detected at this value of times. Must be larger than 1 */
#define PHASE_DET_INPUT_VOLTAGE_RISE_CNT_THRSD        PHASE_DET_INPUT_VOLTAGE_FALL_CNT_THRSD     
#define PFC_VIN_PHASEDETECT_TH                        60.0    /* Input voltage threshold for phase detection [V] */

/*************************************** Voltage&Current Scales ************************************************/
#define PFC_V_DCB_SCALE						433.0	/* MAX measurable DCB voltage [V] */
#define PFC_V_IN_SCALE						433.0	/* MAX measurable input voltage [V] */
#define PFC_I_SCALE							(8.0)  	/* MAX measurable current [A] */
#define PFC_I_HARDWARE_OFFSET                                   2700
#define PFC_I_HARDWARE_LIMIT(OC_A)                              ((uint32_t)((PFC_I_HARDWARE_OFFSET>>3)-(OC_A*4095.0/PFC_I_SCALE)))
/*************************************** Fault thresholds ************************************************/
#define PFC_VIN_OVERVOLT_LIMIT              375.0 	/* Max input voltage peak value [V] */
#define PFC_VIN_UNDERVOLT_LIMIT             120.0 	/* Min input voltage peak value [V] */
#define PFC_OVERVOLT_LIMIT               	420.0 	/* Max DC bus voltage [V] */
#define PFC_UNDERVOLT_LIMIT              	300.0 	/* Min DC bus voltage [V] */
#define PFC_IOVER_LIMIT                     4.0 	/* Max input current [A] */
#define PFC_VIN_FREQOVER_LIMIT              65.0    /* Max frequency on input voltage [Hz] */
#define PFC_VIN_FREQUNDER_LIMIT             45.0    /* Min frequency on input voltage [Hz] */

/*************************************** Relay control ************************************************/
#define PFC_U_DCB_RELAY_OFF                 110.0   /* Relay is turned off when DC bus voltage is below this value [V] */
#define PFC_COEFF_U_DCB_RELAY_ON            0.8     /* Relay can be turned on when DC bus voltage is above Vin_max multiplied with this coefficient */
#define PFC_VIN_THRESHOLD_RELAY_ON          100.0    /* After DC bus reaches a certain value, relay is turned on when AC input voltage is below this value [V] */
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

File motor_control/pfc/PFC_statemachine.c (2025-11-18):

/*
 * Copyright (c) 2013 - 2015, Freescale Semiconductor, Inc.
 * Copyright 2016-2021 NXP
 * All rights reserved.
 *
 * SPDX-License-Identifier: BSD-3-Clause
 */

#include <stdint.h>
#include "fsl_device_registers.h"
#include "PFC_statemachine.h"
#include "Table.h"
#include "common_func.h"
#include "fsl_inputmux.h"
#include "mc_periph_init.h"
/******************************************************************************
* Global variables
******************************************************************************/
/* PFC object including both hardware and software content */
PFCDEF_DRIVE_T     	 gsPFC_Drive;
PFCDRV_PWMVAL            gsPFC_PwmVal;
uint16_t  Fault_Watch=0;
/******************************************************************************
* Static variables
******************************************************************************/
bool_t bPFC_RUN; /* PFC run/stop command */
static  bool_t bEnableCheckDCBusVunder;  /* enabling flag for checking Output voltage under*/
static  bool_t bEnableCheckInputVunder;  /* enabling flag for checking Input voltage under*/
bool_t  bPFCVarInit = 0; /* PFC variables init status flag */
volatile float g_fltPFCCurrentScale, g_fltPFCVoltageScale;
/******************************************************************************
* Local functions
******************************************************************************/

/*------------------------------------
 * User state machine functions
 * ----------------------------------*/
static void PFC_StateFaultFast(void);
static void PFC_StateInitFast(void);
static void PFC_StateStopFast(void);
static void PFC_StateRunFast(void);

static void PFC_StateFaultSlow(void);
static void PFC_StateInitSlow(void);
static void PFC_StateStopSlow(void);
static void PFC_StateRunSlow(void);
/*------------------------------------
 * User state-transition functions
 * ----------------------------------*/
static void PFC_TransFaultInit(void);
static void PFC_TransInitFault(void);
static void PFC_TransInitStop(void);
static void PFC_TransStopFault(void);
static void PFC_TransStopRun(void);
static void PFC_TransRunFault(void);
static void PFC_TransRunStop(void);

/* State machine functions field (in pmem) */
static const sm_app_state_fcn_t s_PFC_STATE_FAST = {PFC_StateFaultFast, PFC_StateInitFast, PFC_StateStopFast, PFC_StateRunFast};

/* State machine functions field (in pmem) */
static const sm_app_state_fcn_t s_PFC_STATE_SLOW = {PFC_StateFaultSlow, PFC_StateInitSlow, PFC_StateStopSlow, PFC_StateRunSlow};

/* State-transition functions field */
static const sm_app_trans_fcn_t msTRANS = {PFC_TransFaultInit, PFC_TransInitFault, PFC_TransInitStop, PFC_TransStopFault, PFC_TransStopRun, PFC_TransRunFault, PFC_TransRunStop};

/* State machine structure declaration and initialization */
sm_app_ctrl_t gsPFC_Ctrl = 
{
	/* gsPFC_Ctrl.psState, User state functions  */
    &s_PFC_STATE_FAST,
    
    /* gsPFC_Ctrl.psState, User state functions  */
    &s_PFC_STATE_SLOW,
    
 	/* gsPFC_Ctrl.psTrans, User state-transition functions */
 	&msTRANS,
 
  	/* gsPFC_Ctrl.uiCtrl, Default no control command */
  	SM_CTRL_NONE,
  	
  	/* gsPFC_Ctrl.eState, Default state after reset */
  	kSM_AppInit 	
};

/*------------------------------------
 * User sub-state machine functions
 * ----------------------------------*/
static void PFC_StateRunSoftstart(void);
static void PFC_StateRunNormal(void);
static void PFC_StateRunLightload(void);

/*------------------------------------
 * User sub-state-transition functions
 * ----------------------------------*/

/* Sub-state machine functions field  */
const pfc_app_state_fcn mPFC_STATE_RUN_TABLE[3] = 
{
    PFC_StateRunSoftstart,
    PFC_StateRunNormal,
    PFC_StateRunLightload
};

sm_app_sub_ctrl_t gsPFC_SubCtrl = 
{
    &mPFC_STATE_RUN_TABLE[0],
    SOFTSTART
};

void SM_StateSubMachineRun(sm_app_sub_ctrl_t *sAppCtrl)
{
    sAppCtrl->pSubState[sAppCtrl->eStateRunSub]();
}

void PFC_FaultDetection(void);

/***************************************************************************//*!
*
* @brief   FAULT detection function
*
* @param   void
*
* @return  none
*
******************************************************************************/
FAST_FUNC_LIB
void PFC_FaultDetection(void)
{
	/* Clearing actual faults before detecting them again  */         
	PFC_FAULT_CLEAR_ALL(gsPFC_Drive.FaultIdPending.R);

	/* DC bus voltage detection */
	if(gsPFC_Drive.sUCtrl.fltUDcBusFilt > gsPFC_Drive.sFaultThresholds.fltUDcBusOver)
	{ 
		gsPFC_Drive.FaultIdPending.B.UDcBusOver = 1;
	}
	else if((gsPFC_Drive.sUCtrl.fltUDcBusFilt < gsPFC_Drive.sFaultThresholds.fltUDcBusUnder)&&(bEnableCheckDCBusVunder))
	{ 
		gsPFC_Drive.FaultIdPending.B.UDcBusUnder = 1;
	}
	
	if(gsPFC_Drive.sUInPeakDetection.bSeveralPeaksDetectedFlag)
	{
		/* AC input voltage detection */
	    if(gsPFC_Drive.sUInPeakDetection.fltUInMax > gsPFC_Drive.sFaultThresholds.fltUInOver)
	    { 
	    	gsPFC_Drive.FaultIdPending.B.UInOver = 1;
	    }
	    else if((gsPFC_Drive.sUInPeakDetection.fltUInMax < gsPFC_Drive.sFaultThresholds.fltUInUnder)&&(bEnableCheckInputVunder))
	    { 
	    	gsPFC_Drive.FaultIdPending.B.UInUnder = 1;
	    }
	    
#if PLL
	    /* AC input frequency detection */
	    if(gsPFC_Ctrl.eState == kSM_AppRun)
	    {
			if(gsPFC_Drive.sPhaseDetector.f16Freq > gsPFC_Drive.sFaultThresholds.f16FreqUInOver)
			{ 
//				gsPFC_Drive.FaultIdPending.B.UInFreqOver = 1;
			}
			else if(gsPFC_Drive.sPhaseDetector.f16Freq < gsPFC_Drive.sFaultThresholds.f16FreqUInUnder)
			{ 
//				gsPFC_Drive.FaultIdPending.B.UInFreqUnder = 1;
			}
	    }
#endif
	}
	/* Phase current detection */
	if(gsPFC_Drive.sICtrlPh1.fltIFdbck > gsPFC_Drive.sFaultThresholds.fltIInOver || gsPFC_Drive.sICtrlPh2.fltIFdbck > gsPFC_Drive.sFaultThresholds.fltIInOver)
	{
		gsPFC_Drive.FaultIdPending.B.IPh1Over = 1;
	}
	
	/* HW Over current detection */
	if(PFC_OVERCURRENT_FAULT())
	{
		gsPFC_Drive.FaultIdPending.B.HW_IOver = 1;
		FLEXPWM0->FSTS |= PWM_FSTS_FFLAG_MASK;
	}
	
	/* HW DC bus over voltage detection */
	if(PFC_OVERVOLTAGE_FAULT())
	{
		gsPFC_Drive.FaultIdPending.B.HW_UDcBusOver = 1;
	}

	/* pass fault to FaultId for recording */
	gsPFC_Drive.FaultId.R |= gsPFC_Drive.FaultIdPending.R;		
}

/***************************************************************************//*!
*
* @brief   FAULT state
*
* @param   void
*
* @return  none
*
******************************************************************************/
static void PFC_StateFaultFast()
{
	PFC_DISABLE_PWM_OUTPUT();
		
	if(gsPFC_Drive.sUCtrl.fltUDcBusFilt < gsPFC_Drive.sUCtrl.fltUDcBusRelayOff)
	{
		RELAY_OFF();
		gsPFC_Drive.sFlag.RelayFlag = 0;
	}
	/* detect faults */
	PFC_FaultDetection();
}
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

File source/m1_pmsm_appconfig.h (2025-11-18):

/*
    * Copyright 2024 NXP 
    *
    * SPDX-License-Identifier: BSD-3-Clause 
*/

/*
    * FILE NAME: ../../source/m1_pmsm_appconfig.h
    * DATE: Thu May 30 2024, 16:10:51
*/

/*
{
    "parameters": {
        "parametersPP": 4,
        "parametersRs": 5,
        "parametersLd": 0.03,
        "parametersLq": 0.06,
        "parametersKe": 0.478,
        "parametersJ": 0.000016,
        "parametersIphNom": 2.5,
        "parametersUphNom": 15,
        "parametersNnom": 1500,
        "parametersImax": 5,
        "parametersUdcbMax": 443.3,
        "parametersUdcbTrip": 400,
        "parametersUdcbUnder": 180,
        "parametersUdcbOver": 420,
        "parametersNover": 1600,
        "parametersNmin": 50,
        "parametersEblock": 30,
        "parametersEblockPer": 2000,
        "parametersNmax": 1600,
        "parametersUdcbIIRf0": 100,
        "parametersCalibDuration": 0.2,
        "parametersFaultDuration": 3,
        "parametersFreewheelDuration": 1.5,
        "parametersScalarUqMin": 8,
        "parametersAlignVoltage": 20,
        "parametersAlignDuration": 4
    },
    "currentLoop": {
        "currentLoopSampleTime": 0.000125,
        "currentLoopF0": 600,
        "currentLoopKsi": 1,
        "currentLoopOutputLimit": 70
    },
    "speedLoop": {
        "speedLoopSampleTime": 0.001,
        "speedLoopF0": 90,
        "speedLoopKsi": 1,
        "speedLoopIncUp": 50,
        "speedLoopIncDown": 50,
        "speedLoopCutOffFreq": 100,
        "speedLoopUpperLimit": 3,
        "speedLoopLowerLimit": -2,
        "speedLoopSLKp": 0.005,
        "speedLoopSLKi": 0.00001,
        "speedLoopManualConstantTunning": false
    },
    "sensorless": {
        "sensorlessBemfObsrvF0": 360,
        "sensorlessBemfObsrvKsi": 1,
        "sensorlessTrackObsrvF0": 30,
        "sensorlessTrackObsrvKsi": 1,
        "sensorlessTrackObsrvIIRSpeedCutOff": 100,
        "sensorlessStartupRamp": 500,
        "sensorlessStartupCurrent": 0.5,
        "sensorlessMergingSpeed": 500,
        "sensorlessMergingCoeff": 150
    }
}
*/

/*
{
    "motorName": "M1p1",
    "motorDescription": ""
}
*/

#ifndef __M1_PMSM_APPCONFIG_H 
#define __M1_PMSM_APPCONFIG_H 

/* PARAMETERS*/
#define M1_MOTOR_PP (4)
#define M1_I_PH_NOM (2.5F)
#define M1_N_NOM (628.319F)
#define M1_I_MAX (5.0F)
#define M1_U_DCB_MAX (443.3F)
#define M1_U_DCB_TRIP (400.0F)
#define M1_U_DCB_UNDERVOLTAGE (180.0F)
#define M1_U_DCB_OVERVOLTAGE (420.0F)
#define M1_N_OVERSPEED (670.206F)
#define M1_N_MIN (20.9440F)
#define M1_E_BLOCK_TRH (30.0F)
#define M1_E_BLOCK_PER (2000)
#define M1_N_MAX (670.206F)
#define M1_CALIB_DURATION (200)
#define M1_FAULT_DURATION (3000)
#define M1_FREEWHEEL_DURATION (1500)
#define M1_SCALAR_UQ_MIN (8.0F)
#define M1_ALIGN_VOLTAGE (20.0F)
#define M1_ALIGN_DURATION (32000)
#define M1_U_MAX (255.939F)
#define M1_FREQ_MAX (106.667F)
#define M1_N_ANGULAR_MAX (2.38732F)
#define M1_UDCB_IIR_B0 (0.0377861F)
#define M1_UDCB_IIR_B1 (0.0377861F)
#define M1_UDCB_IIR_A1 (0.924428F)
#define M1_SCALAR_VHZ_FACTOR_GAIN (0.15F)
#define M1_SCALAR_INTEG_GAIN ACC32(0.0266667)
#define M1_SCALAR_RAMP_UP (0.000416667F)
#define M1_SCALAR_RAMP_DOWN (0.000416667F)
/* CURRENTLOOP*/
#define M1_D_KP_GAIN (221.195F)
#define M1_D_KI_GAIN (53.2959F)
#define M1_Q_KP_GAIN (447.389F)
#define M1_Q_KI_GAIN (106.592F)
#define M1_CLOOP_LIMIT (0.404145F)
/* SPEEDLOOP*/
#define M1_SPEED_RAMP_UP (0.0209440F)
#define M1_SPEED_RAMP_DOWN (0.0209440F)
#define M1_SPEED_LOOP_HIGH_LIMIT (3.0F)
#define M1_SPEED_LOOP_LOW_LIMIT (-2.0F)
#define M1_SPEED_PI_PROP_GAIN (0.00228882F)
#define M1_SPEED_PI_INTEG_GAIN (0.0000647150F)
#define M1_SPEED_IIR_B0 (0.0377861F)
#define M1_SPEED_IIR_B1 (0.0377861F)
#define M1_SPEED_IIR_A1 (0.924428F)
/* SENSORLESS*/
#define M1_OL_START_RAMP_INC (0.0261799F)
#define M1_OL_START_I (0.5F)
#define M1_MERG_SPEED_TRH (209.440F)
#define M1_MERG_COEFF FRAC16(0.00625)
#define M1_I_SCALE (0.979592F)
#define M1_U_SCALE (0.00408163F)
#define M1_E_SCALE (0.00408163F)
#define M1_WI_SCALE (0.000244898F)
#define M1_BEMF_DQ_KP_GAIN (130.717F)
#define M1_BEMF_DQ_KI_GAIN (19.1865F)
#define M1_TO_KP_GAIN (376.991F)
#define M1_TO_KI_GAIN (4.44132F)
#define M1_TO_THETA_GAIN (0.0000397887F)
#define M1_TO_SPEED_IIR_B0 (0.0377861F)
#define M1_TO_SPEED_IIR_B1 (0.0377861F)
#define M1_TO_SPEED_IIR_A1 (0.924428F)
/* USER INPUT START */
/* USER INPUT END */
#endif /* __M1_PMSM_APPCONFIG_H */
